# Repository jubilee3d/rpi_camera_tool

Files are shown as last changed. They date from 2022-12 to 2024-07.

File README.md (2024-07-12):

## Jubilee Camera Inspection Tool
an RP HQ Camera based camera setup that accepts various lenses

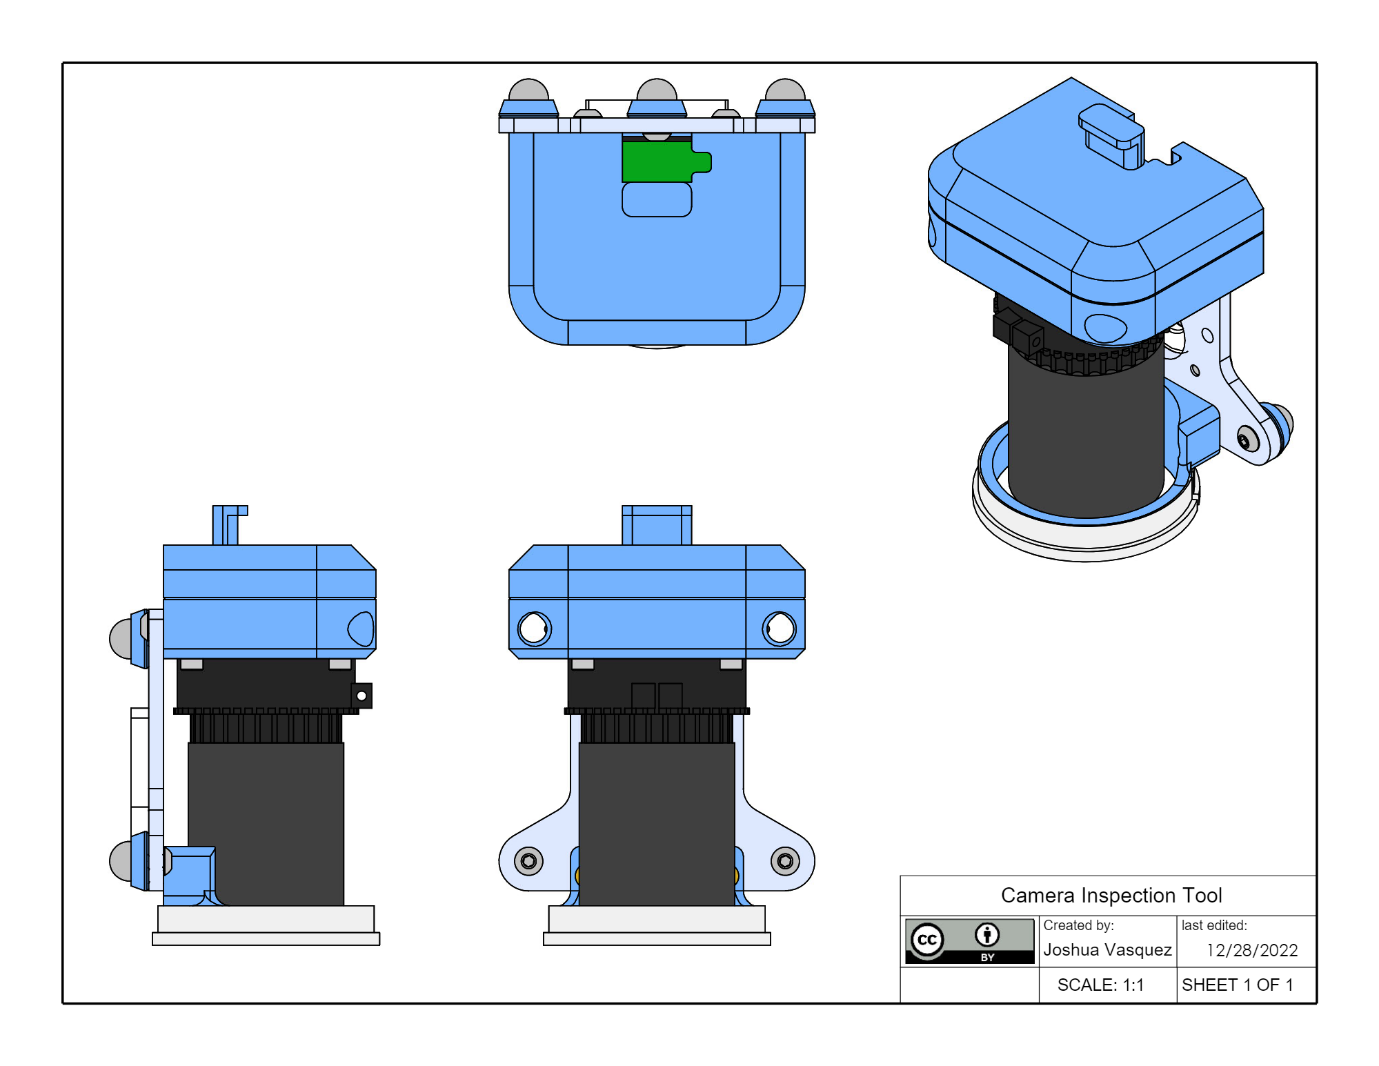
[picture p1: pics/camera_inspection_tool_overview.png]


## Overview
This is a Jubilee-compatible modulare camera inspection tool for inspection applications of items on the bed.

Building one is straightforward too!
Overall cost is ~$100 (USD) plus whatever you're willing to chip in for the lens.

Simply order the parts in the [Shopping List](https://docs.google.com/spreadsheets/d/1ocisjYsW58gLa29wGZ_20qWAk2XupmHxoTtaSmWADwQ/edit?usp=sharing) and follow the step-by-step instructions.

For more information on provisioning this tool for Jubilee, have a look at its corresponding [tool page](https://jubilee3d.com/index.php?title=Camera_Inspection_Tool).

## Specs
* Accepts C and CS-mount lenses with an overall case size of up to 40mm diameter.
* COB LED-based subject lighting solution can be scaled to adjust for different lens sizes.
* compact! Does not sacrifice any of the build volume
* Purchased Parts called out in the [Shopping List](https://docs.google.com/spreadsheets/d/1ocisjYsW58gLa29wGZ_20qWAk2XupmHxoTtaSmWADwQ/edit?usp=sharing)

## Community
This tool is part of the bigger ecosystem of Jubilee-compatible tools that implement the [E3D Toolchanger Coupler](https://github.com/e3donline/ToolChanger) standard.
For more on Jubilee, have a look at the [parent project](https://github.com/machineagency/jubilee) or join the [Discord](https://discord.gg/jubilee).

## Who made this?
This tool was created by [Sonya Vasquez](http://www.doublejumpelectric.com/) formerly at [Machine Agency](http://depts.washington.edu/machines/) at the University of Washington.

## Use the Source!
This tool is licensed with a [Creative Commons Attribution 4.0 Unported License](https://creativecommons.org/licenses/by/4.0/).

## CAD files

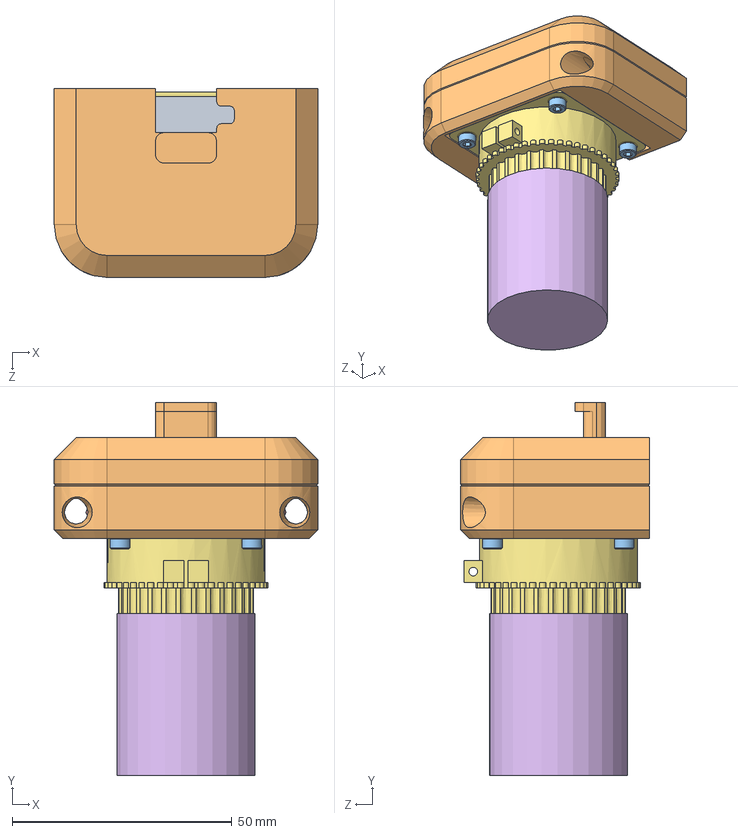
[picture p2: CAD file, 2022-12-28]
cads/solidworks/camera_holder_assembly.SLDASM
60.0 x 84.9 x 43.0 mm
rpi_hq_uvc_adapter_board
printed_base x 2
m2.5_16mm_socket_cap_screw_91292A018 x 4
m3_heat_set_insert_94180A331 x 2
5x9x2_oring x 2
lens_mockup
rasperry_pi_hq_camera

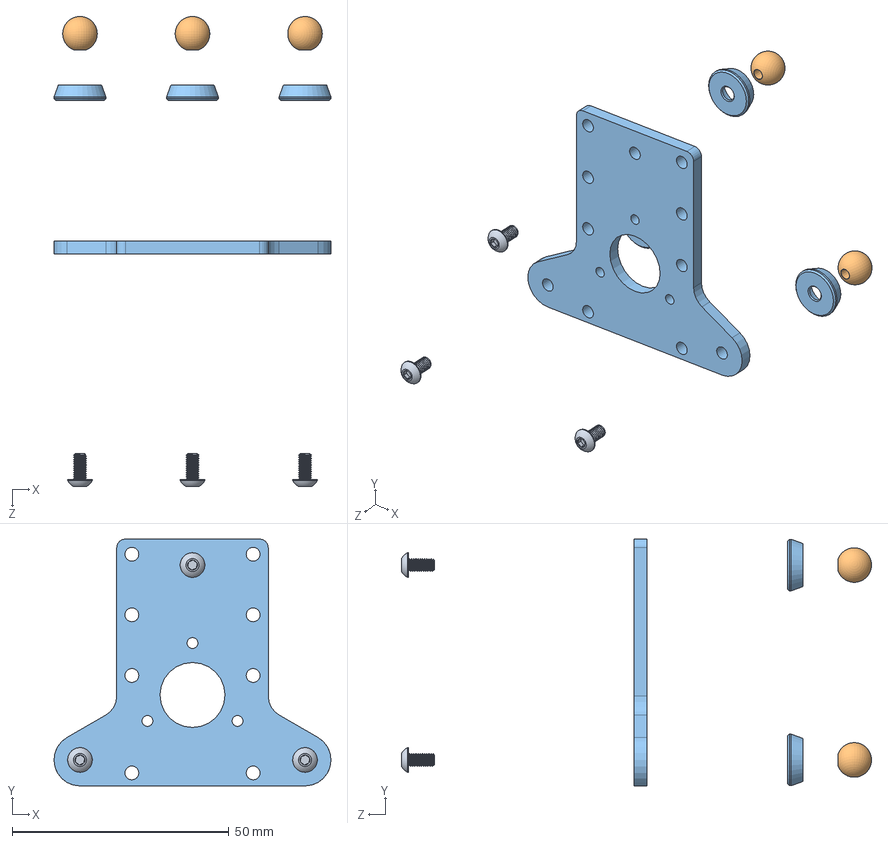
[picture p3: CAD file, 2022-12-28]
cads/solidworks/base_tool_plate_assembly.SLDASM
64.0 x 57.0 x 108.6 mm
m3_6mm_buttonhead_screw_92095A179 x 3
m3_threaded_ball x 3
metal_base_tool_plate x 4

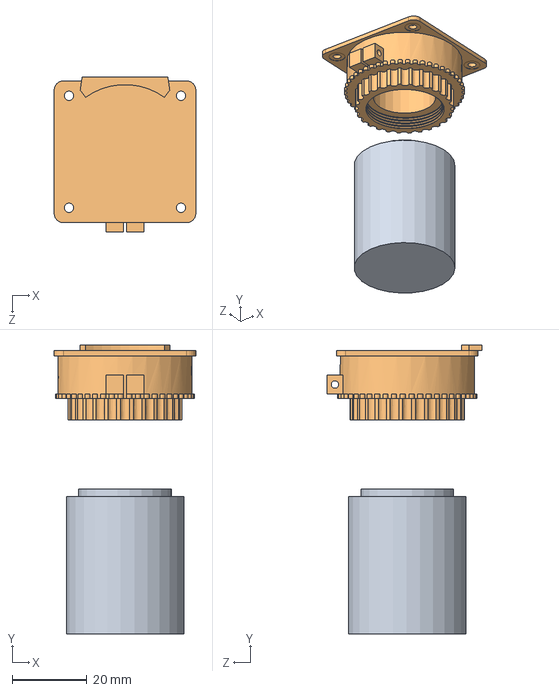
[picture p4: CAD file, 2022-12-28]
cads/solidworks/sensor_with_lens.SLDASM
38.0 x 77.4 x 41.5 mm
lens_mockup
rasperry_pi_hq_camera

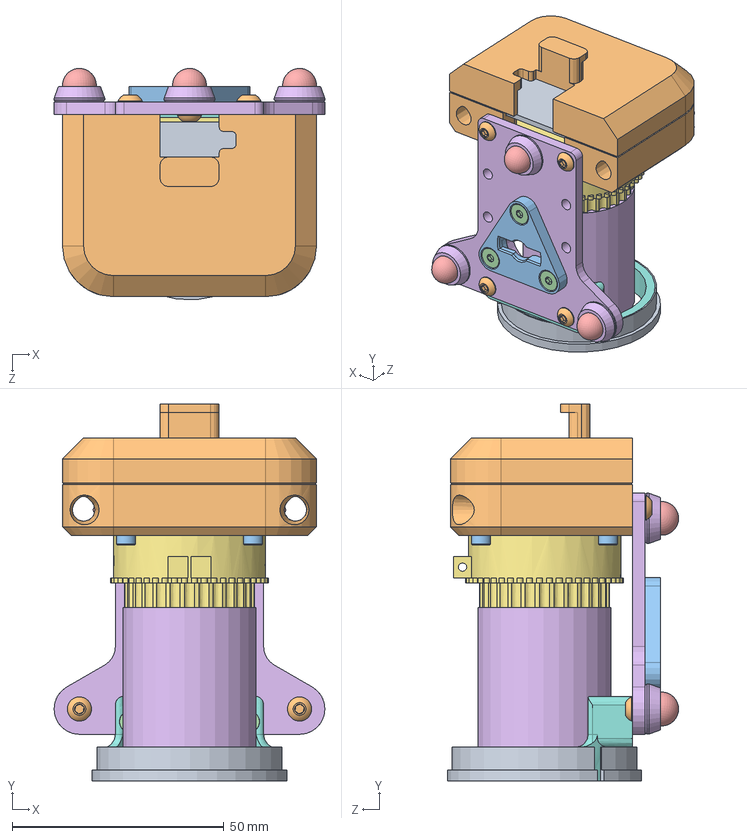
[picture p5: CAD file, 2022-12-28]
cads/solidworks/webcam_mockup.SLDASM
64.0 x 89.0 x 54.6 mm
rpi_hq_uvc_adapter_board
printed_base x 2
m2.5_16mm_socket_cap_screw_91292A018 x 4
m3_heat_set_insert_94180A331 x 4
5x9x2_oring x 2
lens_mockup
rasperry_pi_hq_camera
cob_led_mount
cob_led_strip_cut
m3_6mm_buttonhead_screw_92095A179 x 7
wedge_plate
m3_6mm_flathead_screw_92125A126 x 3
m3_threaded_ball x 3
metal_base_tool_plate x 4

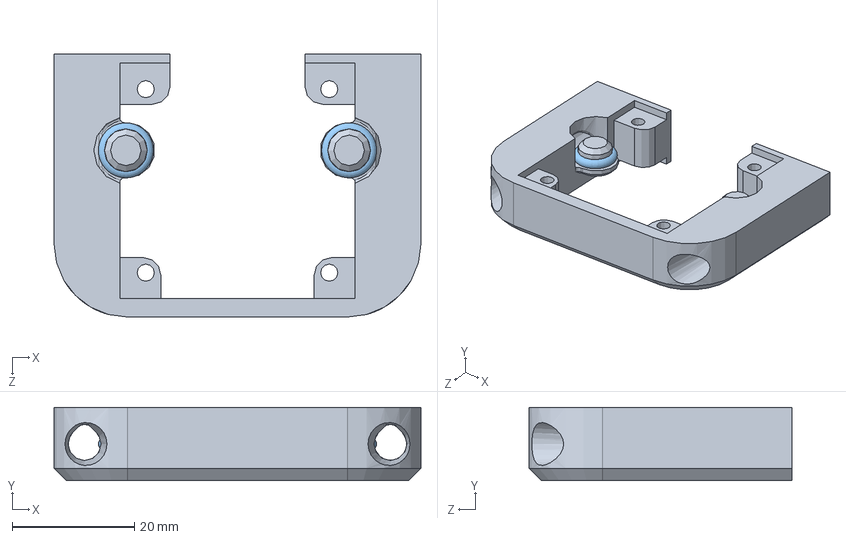
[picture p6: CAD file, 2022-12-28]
cads/solidworks/printed_base_assembly.SLDASM
60.0 x 12.0 x 43.0 mm
printed_base
m3_heat_set_insert_94180A331 x 2
5x9x2_oring x 2

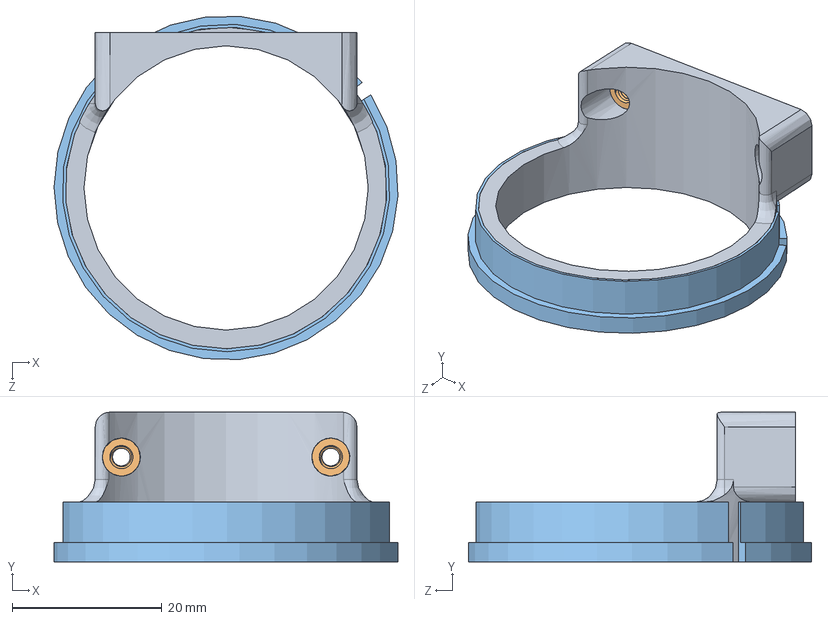
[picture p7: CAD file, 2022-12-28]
cads/solidworks/cob_mount_assembly.SLDASM
46.0 x 20.0 x 45.8 mm
cob_led_mount
m3_heat_set_insert_94180A331 x 2
cob_led_strip_cut

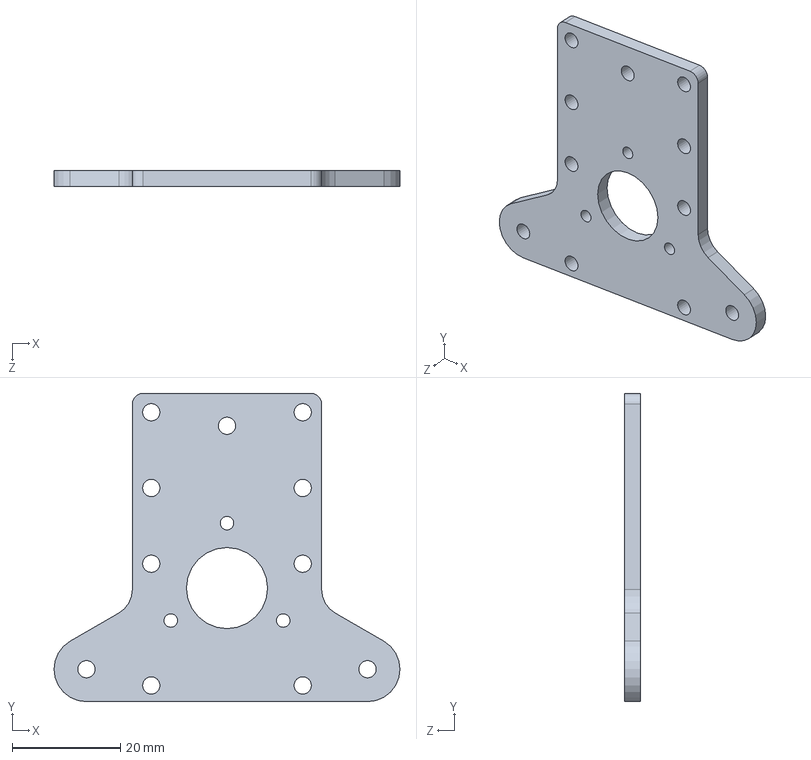
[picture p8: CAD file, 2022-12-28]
cads/solidworks/metal_base_tool_plate.SLDPRT
64.0 x 57.0 x 3.00 mm

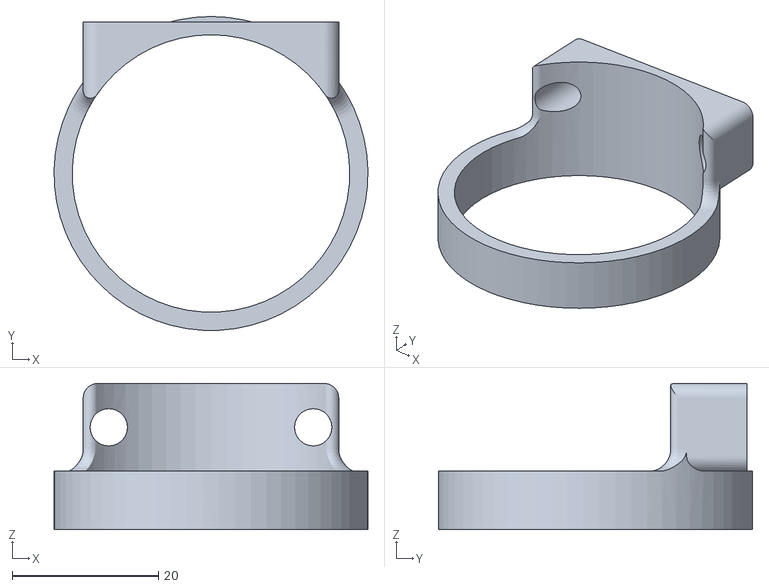
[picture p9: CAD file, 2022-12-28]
fabrication_exports/cob_led_mount.STL
43.0 x 43.0 x 20.0

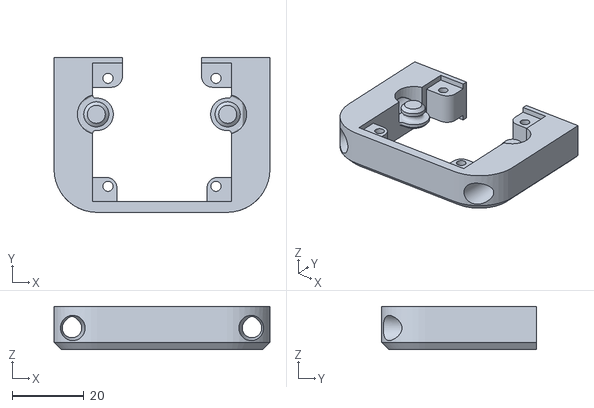
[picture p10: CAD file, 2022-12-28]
fabrication_exports/base.STL
60.0 x 43.0 x 12.0

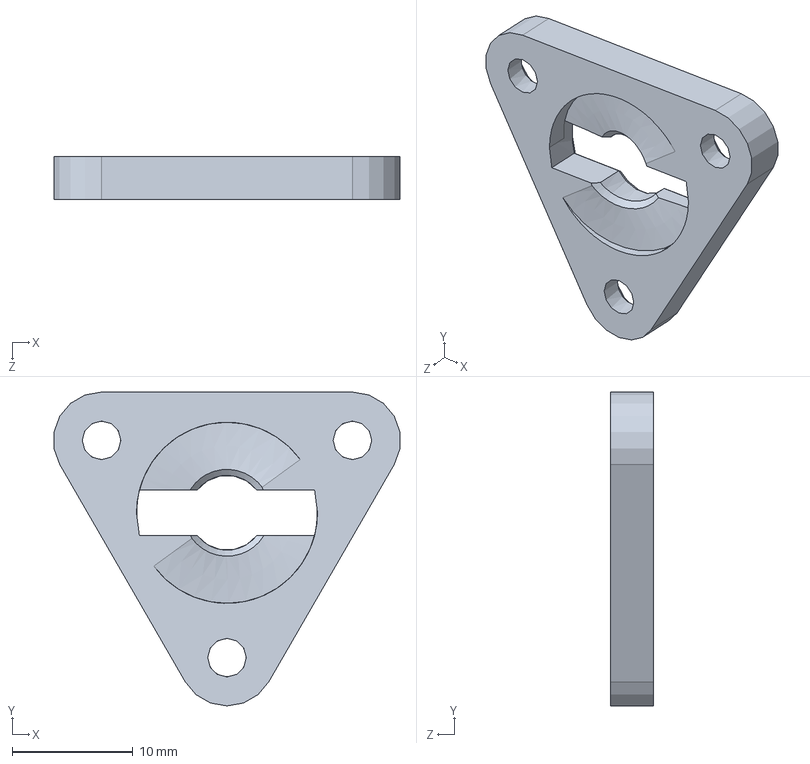
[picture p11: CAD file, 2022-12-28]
cads/solidworks/wedge_plate.SLDPRT
28.7 x 26.0 x 3.60 mm

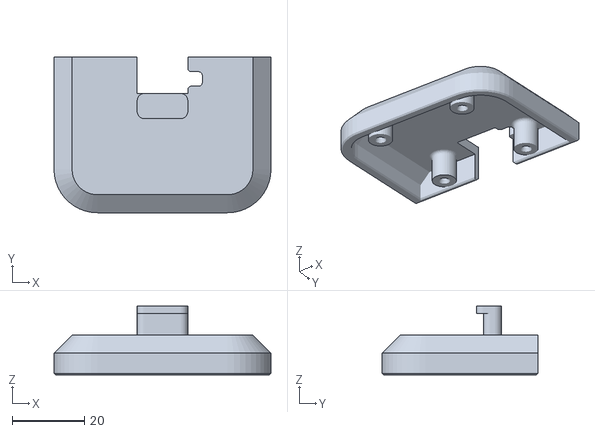
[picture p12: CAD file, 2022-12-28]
fabrication_exports/lid.STL
60.0 x 43.0 x 19.0

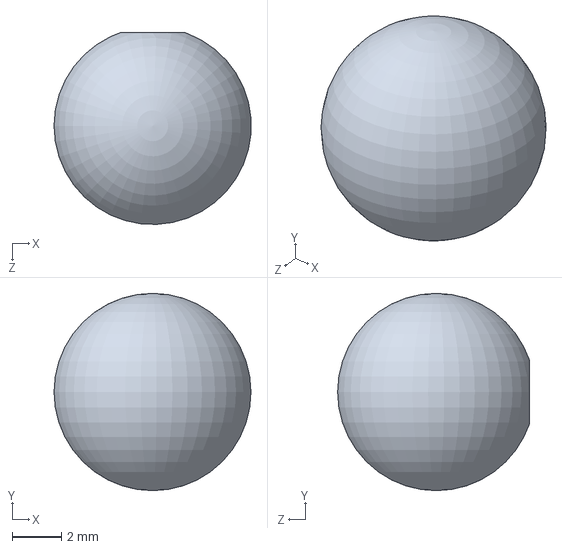
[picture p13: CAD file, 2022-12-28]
cads/solidworks/m3_threaded_ball.SLDPRT
7.99 x 8.00 x 7.78 mm

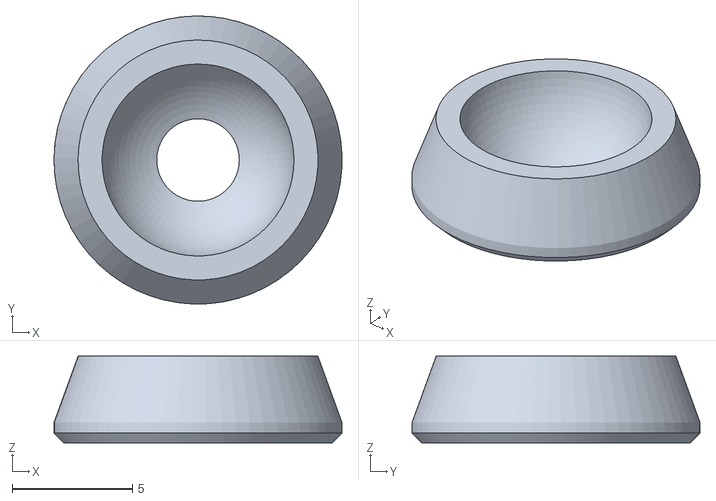
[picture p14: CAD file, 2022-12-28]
fabrication_exports/tool_ball_cup.STL
12.0 x 12.0 x 3.60

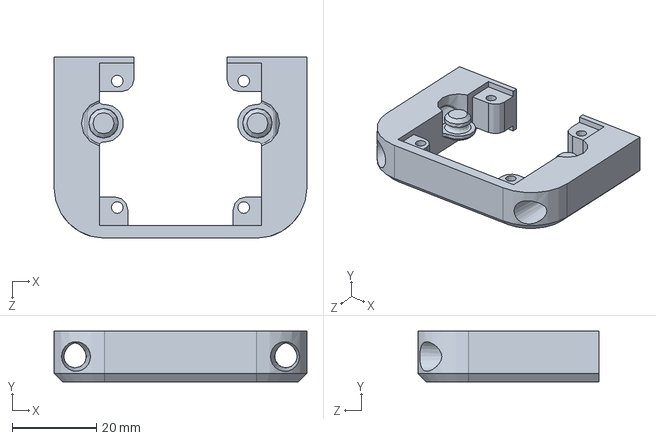
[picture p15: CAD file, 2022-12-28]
cads/solidworks/printed_base.SLDPRT
60.0 x 12.0 x 43.0 mm

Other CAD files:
cads/solidworks/lens_mockup.SLDPRT
cads/solidworks/cob_led_mount.SLDPRT
cads/solidworks/rpi_hq_uvc_adapter_board.SLDPRT
cads/solidworks/5x9x2_oring.SLDPRT
cads/solidworks/cob_led_strip_cut.SLDPRT
cads/solidworks/m2.5_16mm_socket_cap_screw_91292A018.SLDPRT
cads/solidworks/m3_6mm_buttonhead_screw_92095A179.SLDPRT
cads/solidworks/m3_6mm_flathead_screw_92125A126.SLDPRT
cads/solidworks/m3_heat_set_insert_94180A331.SLDPRT
cads/solidworks/rasperry_pi_hq_camera.SLDPRT

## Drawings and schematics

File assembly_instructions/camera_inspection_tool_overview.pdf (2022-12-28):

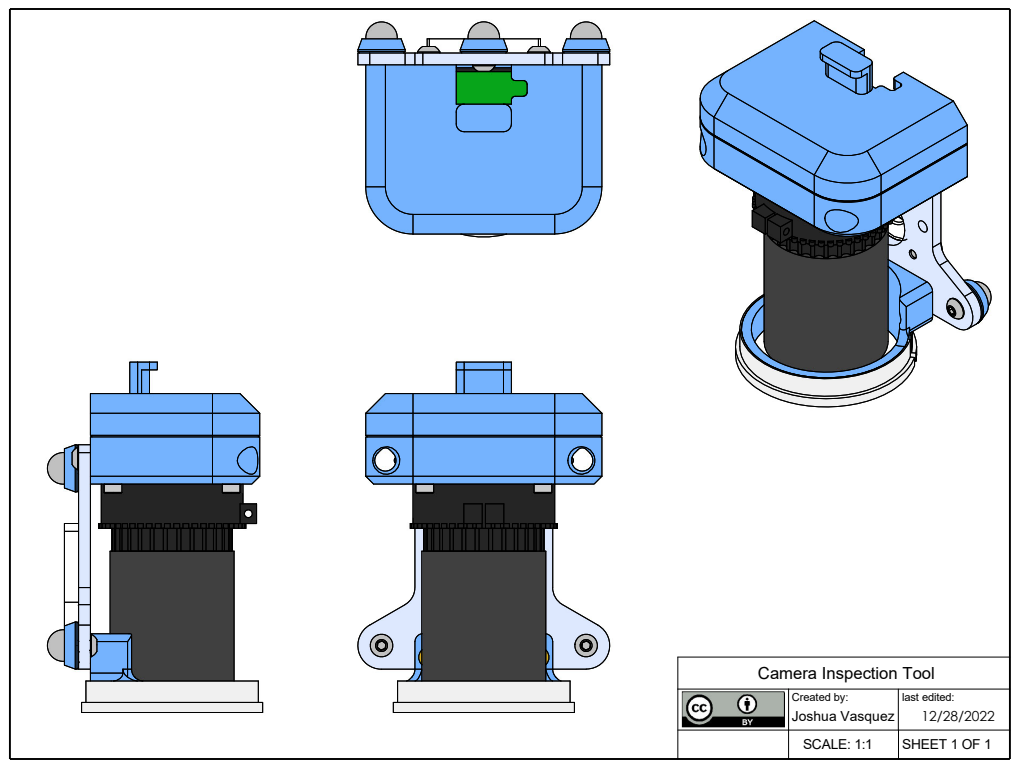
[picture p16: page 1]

Camera Inspection Tool

Created by: Joshua Vasquez | last edited: 12/28/2022

SCALE: 1:1 | SHEET 1 OF 1

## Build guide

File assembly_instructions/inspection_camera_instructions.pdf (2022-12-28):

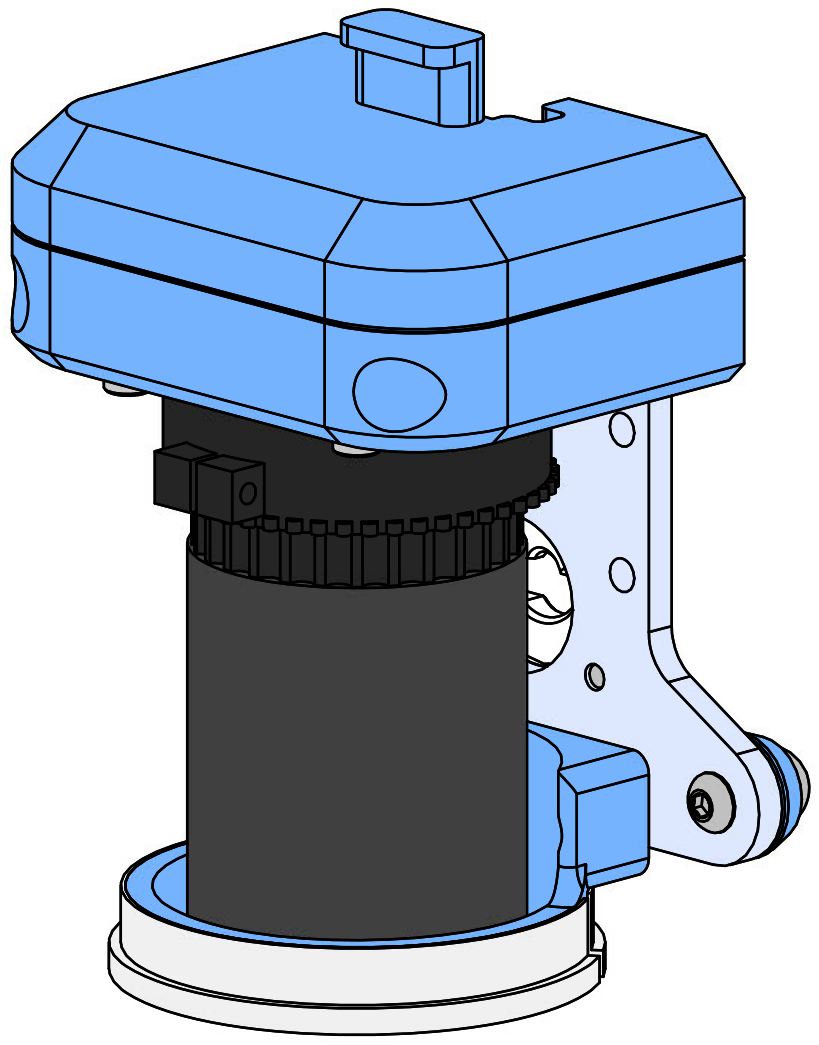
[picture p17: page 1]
Created by:; SHEET 1 OF 11; last edited:; SCALE: 1:1; Joshua Vasquez

Camera Inspection Tool Instructions

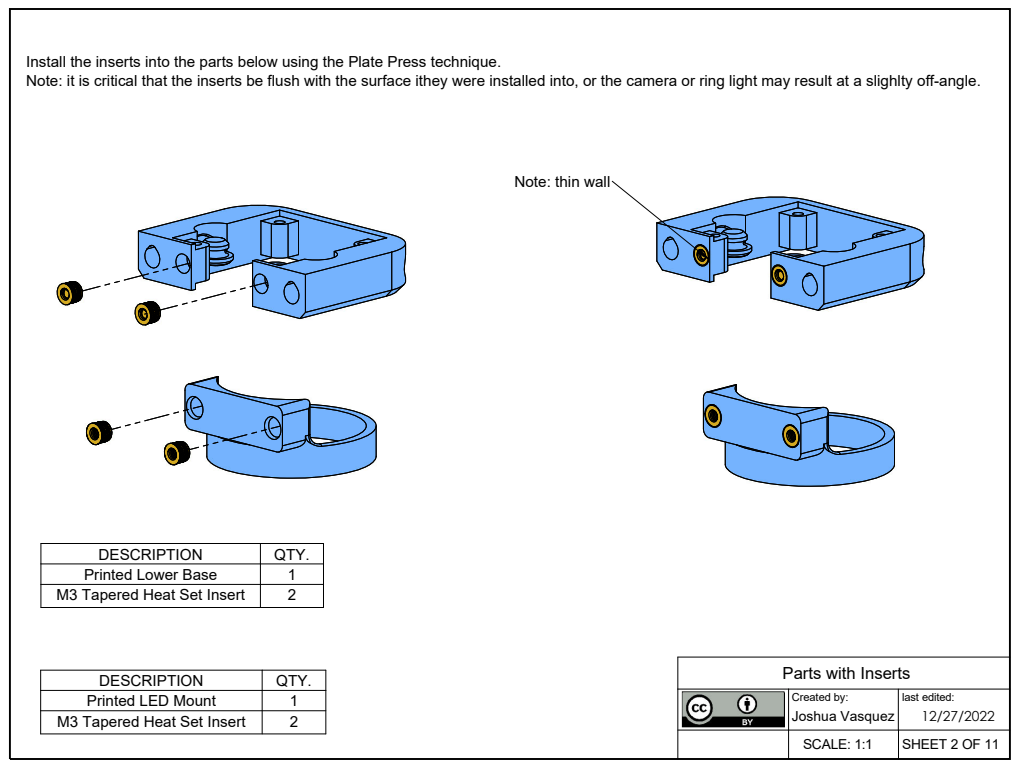
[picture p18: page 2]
Created by:; last edited:; Joshua Vasquez

Install the inserts into the parts below using the Plate Press technique.
Note: it is critical that the inserts be flush with the surface ithey were installed into, or the camera or ring light may result at a slighlty off-angle.

Note: thin wall

DESCRIPTION | QTY.
Printed Lower Base | 1
M3 Tapered Heat Set Insert | 2

Parts with Inserts

Printed LED Mount | 1

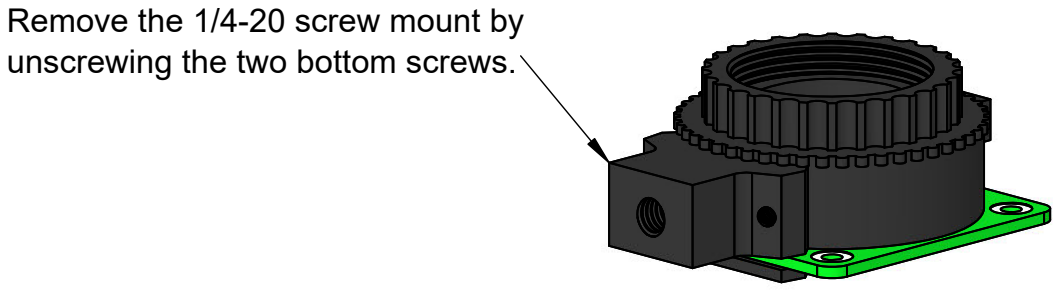
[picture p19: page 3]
last edited: 12/27/2022; Joshua Vasquez; Created by:; IMX4777 Prep

Remove the 1/4-20 screw mount by
unscrewing the two bottom screws.

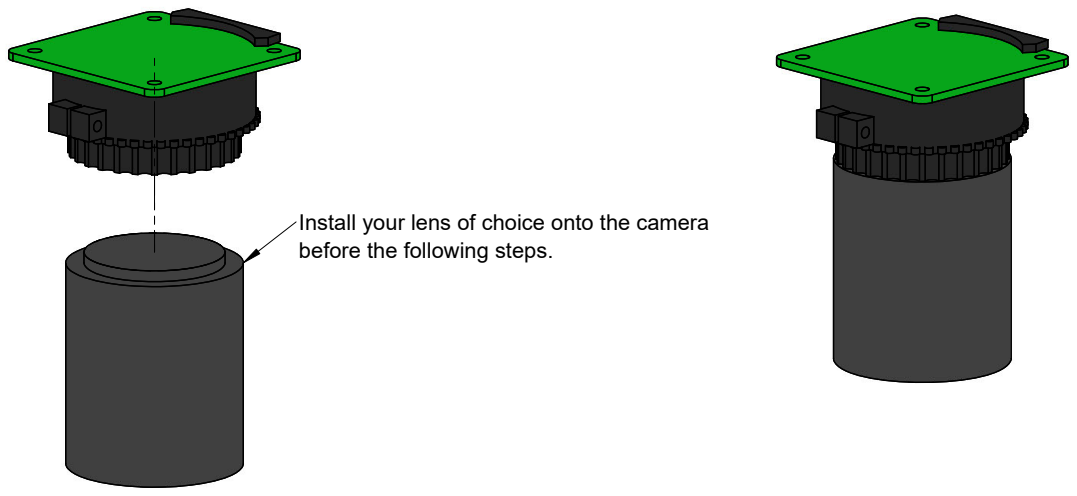
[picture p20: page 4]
Created by:; last edited: 12/27/2022; Joshua Vasquez; Lens Installation

Install your lens of choice onto the camera
before the following steps.

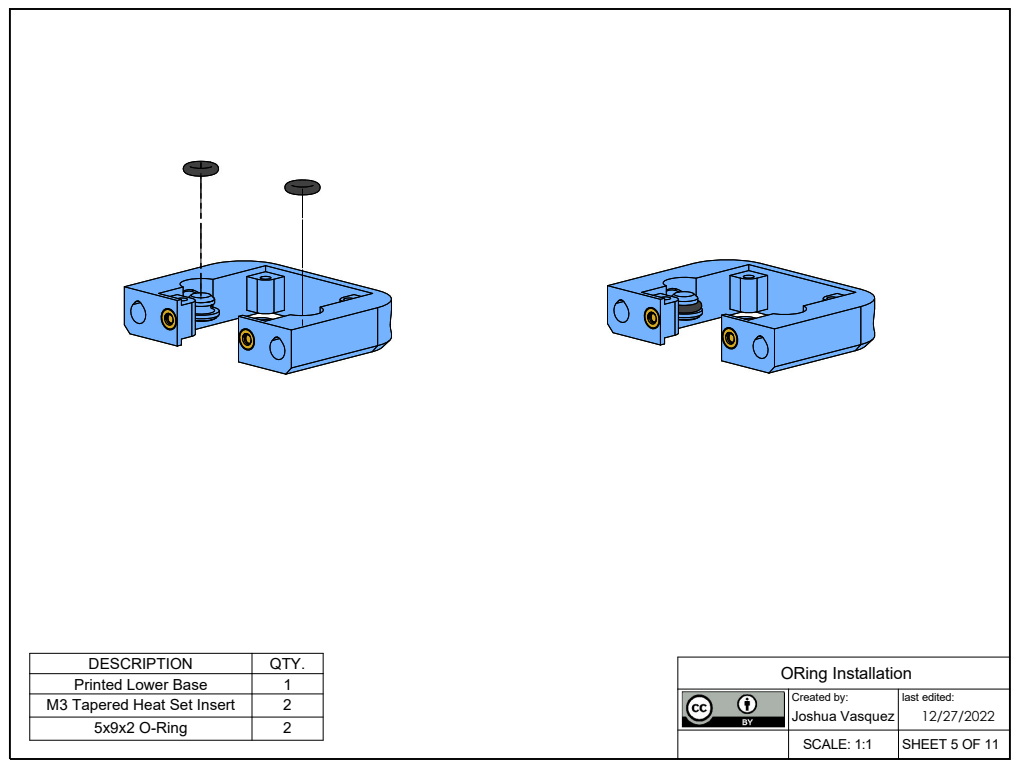
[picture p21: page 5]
last edited: 12/27/2022; Joshua Vasquez; Created by:; ORing Installation

DESCRIPTION | QTY.
Printed Lower Base | 1
M3 Tapered Heat Set Insert | 2
5x9x2 O-Ring | 2

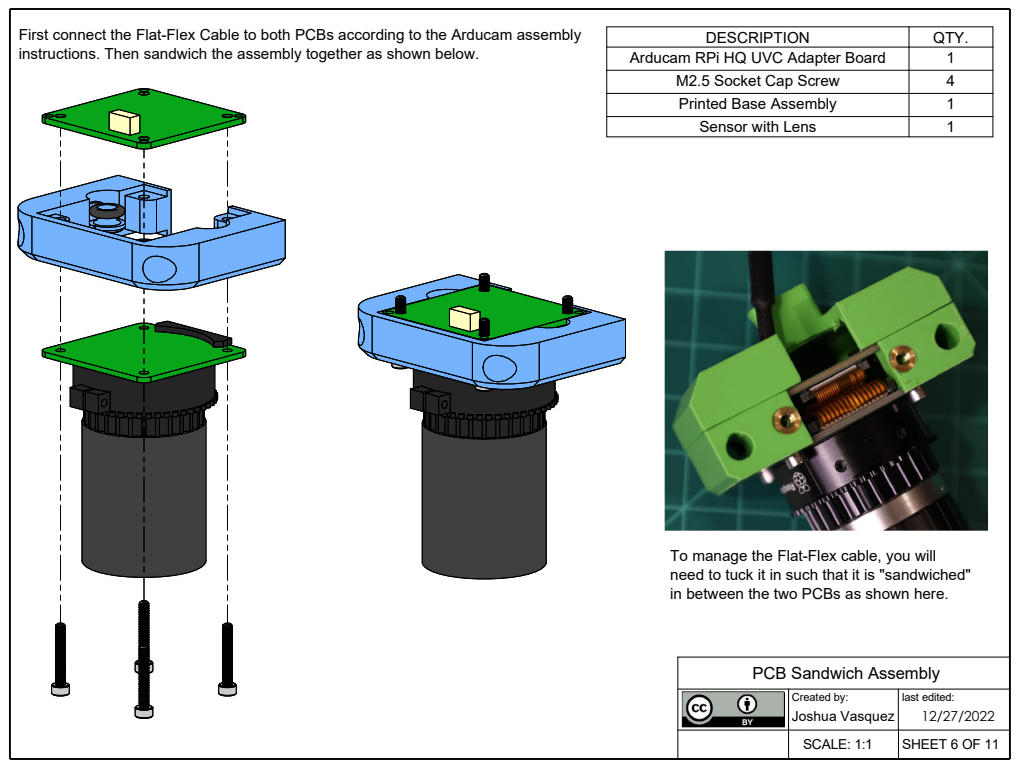
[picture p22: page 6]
last edited: 12/27/2022; Joshua Vasquez; Created by:

First connect the Flat-Flex Cable to both PCBs according to the Arducam assembly
instructions. Then sandwich the assembly together as shown below.

DESCRIPTION | QTY.

Arducam RPi HQ UVC Adapter Board | 1
M2.5 Socket Cap Screw | 4
Printed Base Assembly | 1
Sensor with Lens | 1

To manage the Flat-Flex cable, you will
need to tuck it in such that it is "sandwiched"
in between the two PCBs as shown here.

PCB Sandwich Assembly

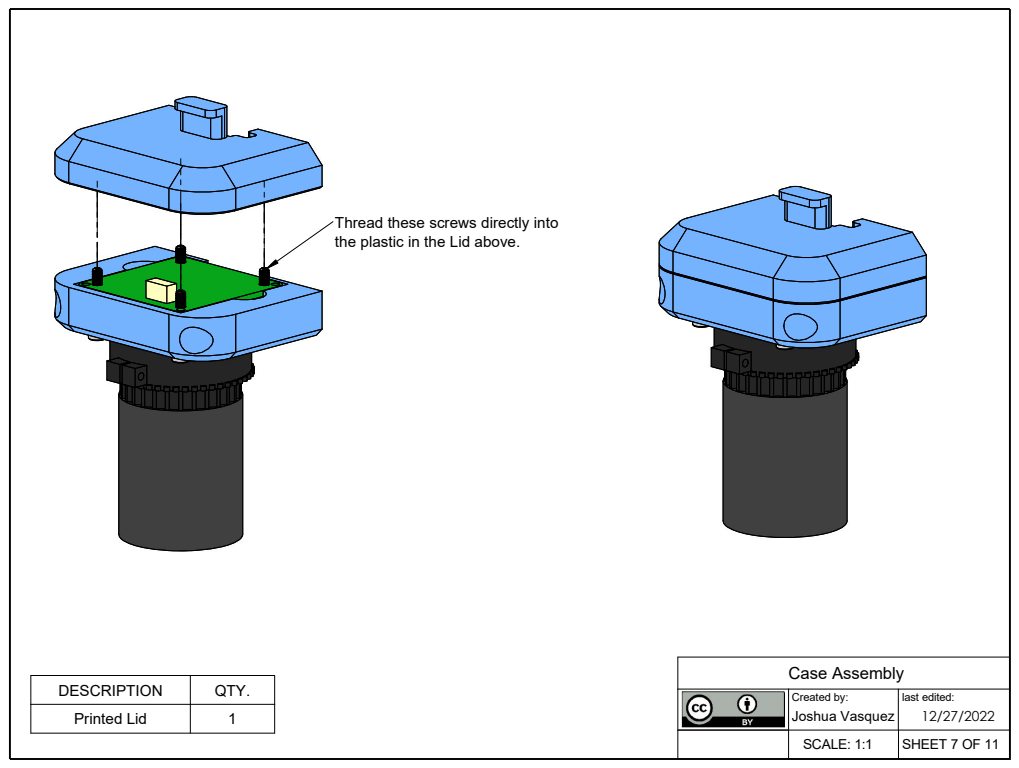
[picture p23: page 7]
Created by:; last edited: 12/27/2022; Joshua Vasquez; Case Assembly

Thread these screws directly into
the plastic in the Lid above.

DESCRIPTION | QTY.
Printed Lid | 1

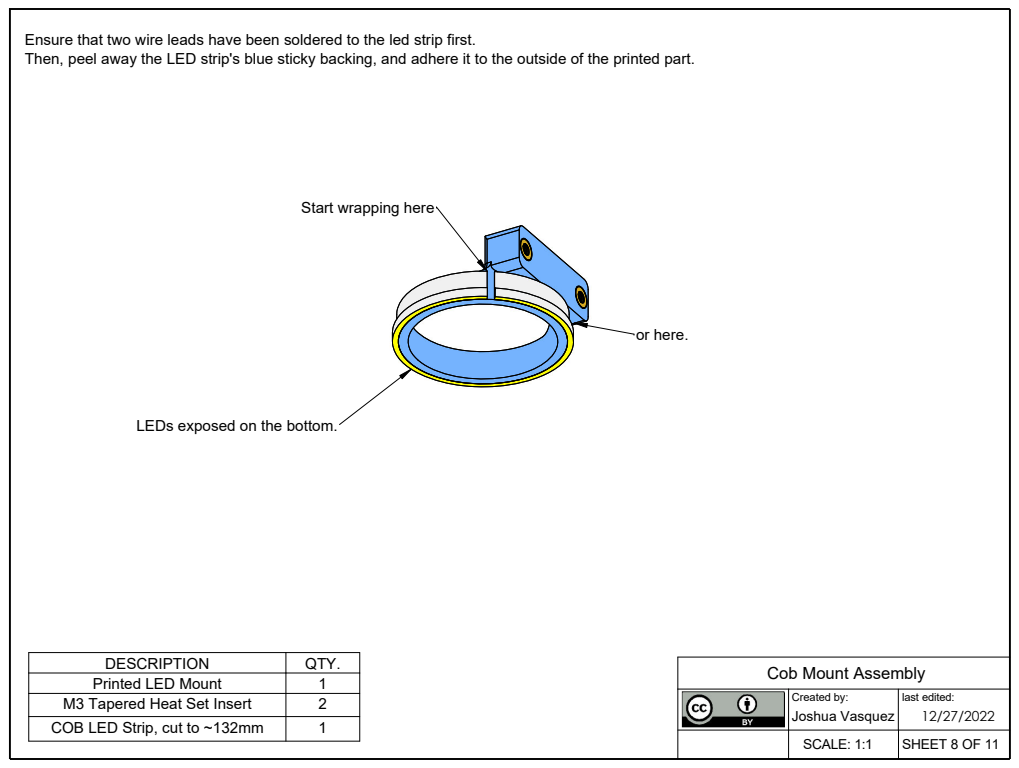
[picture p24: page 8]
or here.; SCALE: 1:1; SHEET 8 OF 11

Ensure that two wire leads have been soldered to the led strip first.
Then, peel away the LED strip's blue sticky backing, and adhere it to the outside of the printed part.

Start wrapping here

LEDs exposed on the bottom.

DESCRIPTION | QTY.
Printed LED Mount | 1
M3 Tapered Heat Set Insert | 2
COB LED Strip, cut to ~132mm | 1

Cob Mount Assembly

Created by: Joshua Vasquez | last edited: 12/27/2022

1 | 2

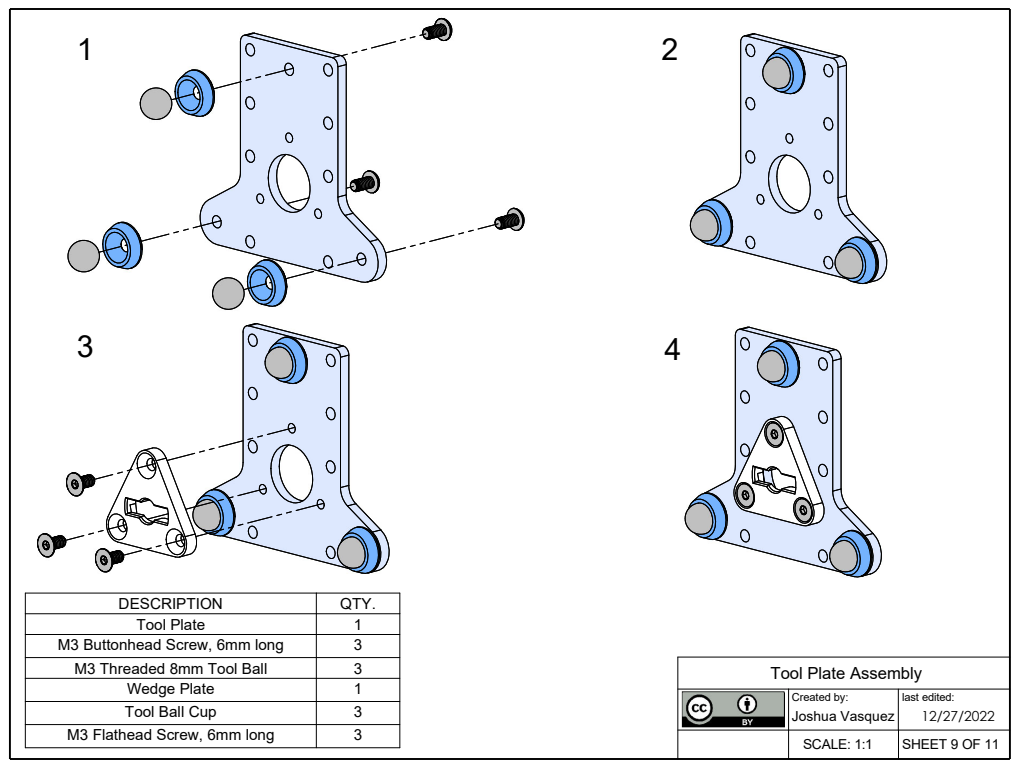
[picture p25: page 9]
Created by:; last edited:; Joshua Vasquez; M3 Threaded 8mm Tool Ball

DESCRIPTION | QTY.
Tool Plate | 1

M3 Buttonhead Screw, 6mm long | 3

Tool Plate Assembly

Wedge Plate | 1
Tool Ball Cup | 3

M3 Flathead Screw, 6mm long | 3

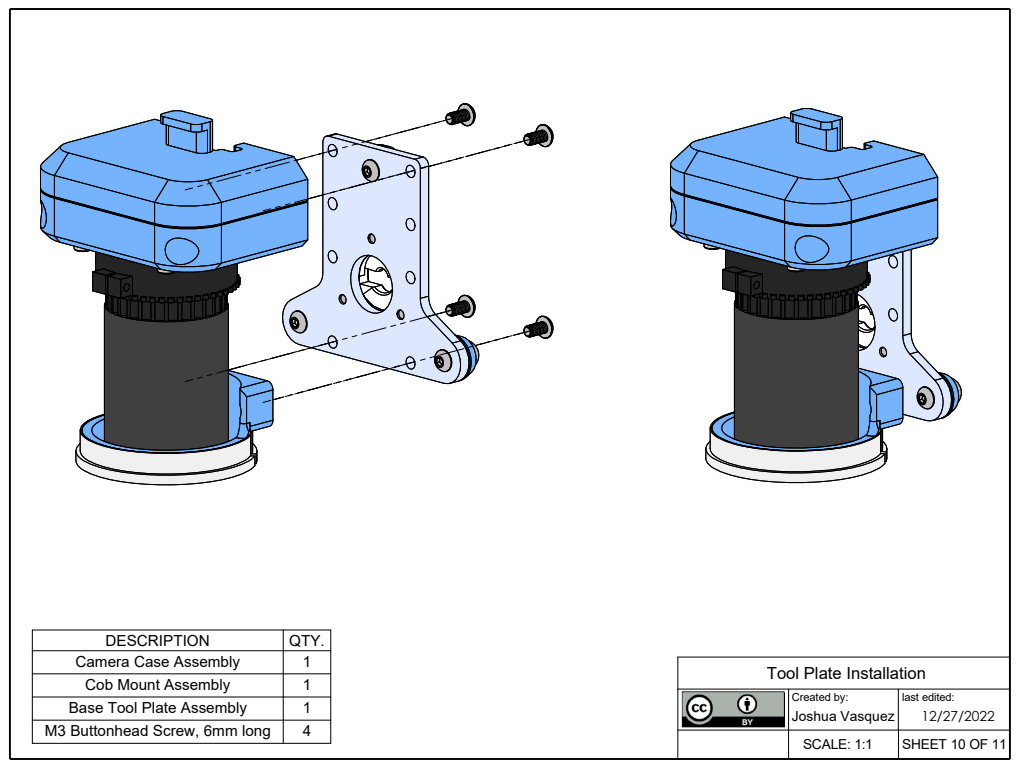
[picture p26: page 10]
Created by:; Joshua Vasquez; last edited:

DESCRIPTION | QTY.
Camera Case Assembly | 1
Cob Mount Assembly | 1
Base Tool Plate Assembly | 1
M3 Buttonhead Screw, 6mm long | 4

Tool Plate Installation

last edited:
12/27/2022
Joshua Vasquez

Created by:

Wire Management

A small zip tie can secure the COB LED wire to the tool plate. | A large (48-in.) zip tie can be used to manage wires extending from the tool to its parking post.
